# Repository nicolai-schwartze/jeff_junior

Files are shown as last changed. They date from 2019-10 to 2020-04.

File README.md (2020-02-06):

# Jeff Junior
This project is part of the FHV Master-Mechatronics course Applied Robotics. 

A 3-axis robot is equipped with 2 cameras and a red laser pointer. 
The robot looks for a green laser dot on a white flip-chart. 
When the green dot is found, the robot aims its red laser at the same position.

The work of this project includes everything, from the design and construction of the robot
to development of the backwards kinematic and computer vision. 

We build this robot on the libraries of:
*	[Dynamixel](https://github.com/ROBOTIS-GIT/DynamixelSDK)
*	[OpenCV](https://opencv.org/)

The backwards kinematic is implemented in C. 
These functions are provided in a dll. 
The computer vision is implemented in python. 

Fun Fact: 
The name originates from a fellow student who (jokingly) insisted, that we bought the robot 
on amazon and ultimately did no work for this project by ourself.

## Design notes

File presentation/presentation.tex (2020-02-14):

\documentclass{beamer}
\usepackage[utf8]{inputenc}

% Beamer Theme, might adapt
% https://hartwork.org/beamer-theme-matrix/
\usetheme{Madrid}
\usecolortheme{beaver}

%for colours e.g. \colorbox
\PassOptionsToPackage{usenames,dvipsnames}{xcolor}
\usepackage{xcolor}

%tables
\usepackage{longtable}
\usepackage{tabularx} 

\newcommand{\linebreakcellright}[2][c]{%
	\begin{tabular}[#1]{@{}r@{}}#2\end{tabular}}

\newcommand{\linebreakcellleft}[2][c]{%
	\begin{tabular}[#1]{@{}l@{}}#2\end{tabular}}

\newcommand{\linebreakcellcentre}[2][c]{%
	\begin{tabular}[#1]{@{}c@{}}#2\end{tabular}}

%Inline Code Snippets
\usepackage{listings}
\usepackage{color}

\definecolor{mygreen}{rgb}{0,0.6,0}
\definecolor{mygray}{rgb}{0.5,0.5,0.5}
\definecolor{mymauve}{rgb}{0.58,0,0.82}

\lstset{ 
	backgroundcolor=\color{white},   % choose the background color; you must add \usepackage{color} or \usepackage{xcolor}; should come as last argument
	basicstyle=\small,        % the size of the fonts that are used for the code
	breaklines=true,                 % sets automatic line breaking
	commentstyle=\color{mygreen},    % comment style
	extendedchars=true,              % lets you use non-ASCII characters; for 8-bits encodings only, does not work with UTF-8
	keepspaces=true,                 % keeps spaces in text, useful for keeping indentation of code (possibly needs columns=flexible)
	keywordstyle=\color{blue},       % keyword style
	language=Octave,                 % the language of the code
	morekeywords={parfor,pararrayfun, innerES},            % if you want to add more keywords to the set
	numbersep=5pt,                   % how far the line-numbers are from the code
	numberstyle=\tiny\color{mygray}, % the style that is used for the line-numbers
	rulecolor=\color{black},         % if not set, the frame-color may be changed on line-breaks within not-black text (e.g. comments (green here))
	showspaces=false,                % show spaces everywhere adding particular underscores; it overrides 'showstringspaces'
	showstringspaces=false,          % underline spaces within strings only
	showtabs=false,                  % show tabs within strings adding particular underscores
	stepnumber=1,                    % the step between two line-numbers. If it's 1, each line will be numbered
	stringstyle=\color{mymauve},     % string literal style
	tabsize=2,	                   	 % sets default tabsize to 2 spaces
}

% for pseudocode
\usepackage{amsmath}
\usepackage{algorithm}
\usepackage[noend]{algpseudocode}
\makeatletter
\def\BState{\State\hskip-\ALG@thistlm}
\makeatother

\title[jeff\textunderscore junior]{3 Axis Robot following a Laserpointer by using Stereovision and Templatematching}

\author[jwu, nsc]{Johannes Wüstner, Nicolai Schwartze}

\date{\today}

\begin{document}
\maketitle

\section{Introduction}
\frame{\tableofcontents}

\begin{frame}{Project Description}

\begin{itemize}
	\item construct a 3-axis robot with camera/laser tool
	\item calculate the backwards kinematic 
	\item program robot functions in C-DLL
	\item calibrate 3D camera system
	\begin{itemize}
		\item camera projection matrix
		\item hand-eye calibration
	\end{itemize}
	\item detect laser point on white flip-chart
	\item computer vision using OpenCV and Python
	\item drive with red robot laser to green user laser
\end{itemize}

\end{frame}

\section{Design}
\frame{\tableofcontents[currentsection]}

\begin{frame}{Task}
\begin{itemize}
	\item design a 3-axis robot in SolidWorks \\
	\item assemble the parts \\
	\item using Dynamixel MX-64AT motors \\
	\item attach camera/laser tool \\
\end{itemize}

\end{frame}

\begin{frame}{Result}

\begin{center}
	\begin{tabular}{ c c }
		   & 
		   
	\end{tabular}
\end{center}

\end{frame}

\section{Calculation}
\frame{\tableofcontents[currentsection]}

\begin{frame}{Task}

\begin{itemize}
	\item generate robot-backwards kinematic \\
	\item develop equation for setting angle of motor \\
	\item establish transformation matrix for hand-eye coordination \\
\end{itemize}

\end{frame}

\begin{frame}{Problem}

\begin{itemize}
	\item backwards kinematic
	\begin{itemize}
		\item establish DH parameter $\rightarrow$ transformation matrix TCP to robot base
	\end{itemize}
	\item setting motor angle
	\begin{itemize}
		\item only need two DOF $\rightarrow$ overdetermined
	\end{itemize}
	\item hand-eye coordination
	\begin{itemize}
		\item estimate the right distance camera to TCP
	\end{itemize}
\end{itemize}

\end{frame}

\begin{frame}{Solution I}

\begin{columns}[T] % align columns
	\begin{column}{.48\textwidth}
		\begin{center}
			
		\end{center}
		
	\end{column}%
	\hfill%
	\begin{column}{.45\textwidth}
		~\\~\\~\\
		\begin{center}
			\begin{tabular}{ c c c c c }
				$i$ & $\alpha_{i-1}$ & $a_{i-1}$ & $d_i$ & $\theta_{i-1}$\\ 
				\hline
				1 & 0 & 0 & 100 & $\theta_0$\\  
				2 & -90 & 50 & 0 & $\theta_1 - 90$\\ 
				3 & 0 & 100 & 0 & $\theta_2 + 180$\\ 
				F & 90 & 0 & 68 & $0$
			\end{tabular}
		\end{center}

	\end{column}%
\end{columns}

\end{frame}

\begin{frame}{Solution II}

\begin{equation}
\theta_0 = arctan(\frac{Y_0}{X_0})
\end{equation}

\begin{equation}
\theta_1 = 0.0
\end{equation}

\begin{equation}
\theta_2 = -1 \cdot arctan \left( \frac{ Z_0 - 100 - 100 cos(\theta_1)}{\sqrt{X_{0}^{2} + Y_{0}^{2}} - 50 - 100 sin(\theta_1)} \right)
\end{equation}

\end{frame}

\section{Camera Calibration}
\frame{\tableofcontents[currentsection]}

\begin{frame}{Task}

\begin{itemize}
	\item calculate camera matrix for both single cameras \\
	\item estimate translation and rotation between cameras \\
\end{itemize}

\end{frame}

\begin{frame}{Problem}

\begin{itemize}
	\item unstable against repetition \\
	\item chessboard must not have the same hight and width \\
	\item three quality control measures: 
	\begin{itemize}
		\item plausibility: translation vector between cameras
		\item measure actual 3D points 
		\item comparison with matlab
	\end{itemize}
\end{itemize}

\end{frame}

\begin{frame}{Solution}
\begin{center}

\end{center}
\end{frame}

\section{Laser Point Detection}
\frame{\tableofcontents[currentsection]}

\begin{frame}{Task}

\begin{itemize}
	\item detect green laser point
	\item detect red laser point (not used; would be helpful for controller)
\end{itemize}

\end{frame}

\begin{frame}{Problem}

\begin{itemize}
	\item first idea: use threshold for colour of laser
	\item detect contour 
	\item calculate centre of mass 
	\item problem: unstable against other lighting conditions
	\bigskip
	\item red laser point too small
	\item use laser with adjustable focal length 
\end{itemize}

\end{frame}

\begin{frame}{Solution}

\begin{itemize}
	\item use template matching
	\item created template calibration app before every run
	\item more stable against lighting conditions
	\item but can only work on specified background (like a flip-chart)
\end{itemize}
~\\
using the CV\textunderscore TM\textunderscore CCOEFF\textunderscore NORMED

\begin{equation}
R(x,y) = \frac{\sum_{x',y'} (T'(x',y') \cdot I'(x + x', y + y'))}{\sqrt{\sum_{x',y'} T'(x',y')^{2} \cdot \sum_{x',y'} I'(x + x', y + y')^{2}}}
\end{equation}
~\\
also works for coloured images, this equation is applied for every channel

\end{frame}

\section{Conclusion, Further Work}
\frame{\tableofcontents[currentsection]}

\begin{frame}{Summary, Further Work}

\begin{itemize}
	\item works (sort of) but slow convergence
	\item overshooting 
	\item resting offset 
	\item not using $\theta_1$
	\item 3 USB ports needed - opencv does not find camera on hub
	\item red laser uses loads of batteries $\frac{220 mAh}{45 mA} = 4.8 h$
	\bigskip
	\item implement controller 
	\item correct laser offset to align with axis $\theta_2$
	\item use undistort before calculateing 3D point
	\item power supply for laser
\end{itemize}

\end{frame}

\end{document}

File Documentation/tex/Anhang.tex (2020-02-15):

\documentclass[./\jobname.tex]{subfiles}
\begin{document}

\chapter{Drawings}

\includepdf[page=-]{../img/pdf/AKT L 3x30x80x30.pdf}
\includepdf[page=-]{../img/pdf/AKT U 3x48x40x48x90.pdf}
\includepdf[page=-]{../img/pdf/AKT U 3x73x46x73x90.pdf}
\includepdf[page=-]{../img/pdf/AKT Z 3x40x20x42_5x50.pdf}

\chapter{Motor Parameters}

\begin{table}[H]
	\centering
	\noindent\adjustbox{max width=\linewidth}{
		\begin{tabular}{|c|c|c|c|}
			\hline
			parameter & axis 0 & axis 1 & axis 2 \\
			\hline
			home offset & 2288 & 2060 & 3074 \\
			\hline
			min angle & 1580 & 2060 & 1650 \\
			\hline
			max angle & 3000 & 3200 & 3100 \\
			\hline
			max velocity & 20 & 20 & 20 \\
			\hline
			home & 2290 & 2060 & 3072 \\
			\hline
		\end{tabular}
	}
	\unterschrift{table of motor parameters}{}{}
	\label{tab:motor_param}
\end{table}

\end{document}

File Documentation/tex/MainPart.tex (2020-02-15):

% !TeX spellcheck = <none>
\documentclass[./\jobname.tex]{subfiles}

\begin{document}
\definecolor{light-gray}{gray}{0.9}

\chapter{Task Description}

This project is about constructing and building a 3-axis robot. The robot is equipped with two cameras and a red laser-pointer. The user can take a green laser-pointer to direct the robot into a different position. In order to avoid permanent sight-damage, the robot should avoid shining the laser into faces of surrounding humans. The following list contains the main working steps:

\begin{itemize}
	\item design and construct the 3-axis robot 
	\item manufacture and assemble the robot parts 
	\item develop the backwards kinematic 
	\item implement the backwards kinematic in C and compile to DLL 
	\item find green laser point in 3D stereo image with OpenCV in Python 
	\item drive the red laser point of the robot to the green laser point of the human
	\item planned but optional: 
	\begin{itemize}
		\item plan path from current position to green laser position 
		\item implement controller to correct deviance between red and green laser point 
		\item avoid human faces along the way
	\end{itemize}
	
\end{itemize}

\chapter{Design}

The robot consists of 3 Dynamixel MX-64AT motors, 2 Microsoft HD 3000 lifecam and a laser module DB635-1-3-FA(14x45)-ADJ from Picotronic. Aluminium frames are attached to the motors to build the framework of the robot. The cameras and laser-pointer are connected with aluminium brackets to the robot. The design of the robot and its components is established with SolidWords. The whole robot is mounted on aluminium profiles to improve the handling and to store of the electrical hardware. Beside the cables, a power supply for the motors and laser pointer, an emergency stop button and communication components for the motors are required. The cameras are directly connected to the laptop or computer via the USB ports. This means that the laptop requires 3 USB sockets. A connection via a USB-Hub failed as the OpenCV library could not find the cameras. \\
The table \ref{tab:camera_before_after} shows how the cameras were modified in order to properly attach them to the robot tool. \\
The table \ref{tab:3d_rander} displays a 3D render of the completely assembled robot.\\
Finally, the finished robot can be seen in figure \ref{fig:final_assemgly}

\begin{table}[H]
	\centering
	\noindent\adjustbox{max width=\linewidth}{
		\begin{tabular}{c c}
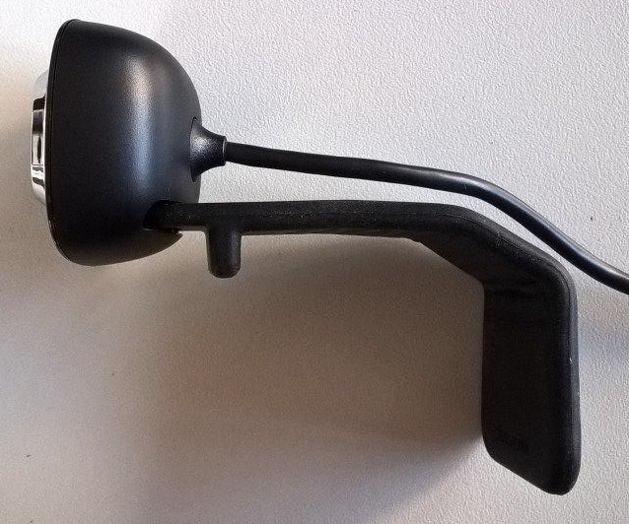
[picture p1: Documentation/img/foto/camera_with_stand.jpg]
			
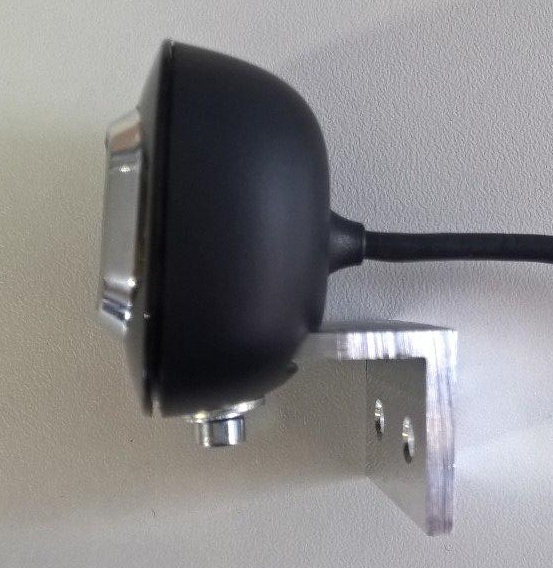
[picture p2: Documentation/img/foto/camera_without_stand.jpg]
			
		\end{tabular}
	}
	\unterschrift{comparison of the cameras before and after modification}{}{}
	\label{tab:camera_before_after}
\end{table}

\begin{table}[H]
	\centering
	\noindent\adjustbox{max width=\linewidth}{
		\begin{tabular}{c c}
			
			
		\end{tabular}
	}
	\unterschrift{3D render of the assembled robot in SolidWorks}{}{}
	\label{tab:3d_rander}
\end{table}

\begin{figure}[H]
	\centering
	\noindent\adjustbox{max width=\linewidth}{
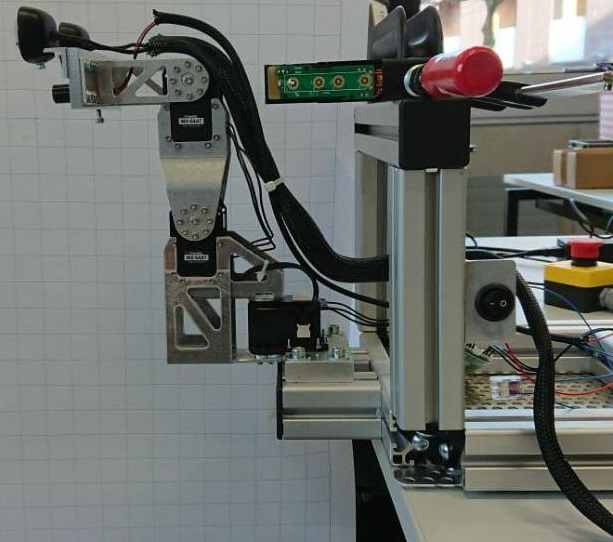
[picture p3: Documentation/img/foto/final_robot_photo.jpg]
		
	}
	\unterschrift{final assembly of the robot}{}{}
	\label{fig:final_assemgly}
\end{figure}

\chapter{Calculation}
This chapter describes the mathematical formulations that are needed to control the robot. This includes the backwards kinematics as well as the formulas for setting $\theta_{0,1,2}$. 

\section{Backwards Kinematic}

The following figure \ref{fig:robot_coord} shows the coordinate systems that are used to get the link parameters shown in table \ref{tab:link_params} below. The link parameters are established using the Deviant Hartenberg convention mentioned in \cite[p. 70- 79]{Craig2018}.

With the knowledge of the link parameters, the transformation matrices are generated in the next step. The full matrix can be seen in equation \ref{eq:transformationmatrix}

\begin{figure}[H]
	\centering
	\noindent\adjustbox{max width=\linewidth}{
		
	}
	\unterschrift{robot axis coordinate systems used to calculate the link parameters}{}{}
	\label{fig:robot_coord}
\end{figure}

\begin{table}[H]
	\centering
	\noindent\adjustbox{max width=\linewidth}{
		\begin{tabular}{|c|c|c|c|c|}
			\hline
			$i$ & $\alpha_{i-1}$ & $a_{i-1}$ & $d_i$ & $\theta_{i-1}$\\ 
			\hline
			1 & 0 & 0 & 100 & $\theta_0$\\  
			2 & -90 & 50 & 0 & $\theta_1 - 90$\\ 
			3 & 0 & 100 & 0 & $\theta_2 + 180$\\ 
			F & 90 & 0 & 68 & $0$ \\
			\hline
		\end{tabular}
	}
	\unterschrift{table of link parameters}{}{}
	\label{tab:link_params}
\end{table}

\begin{equation}
\label{eq:transformationmatrix}
\begin{split}
& T =  \\
& \begin{bmatrix}
-c0c1s2 -c0c2s1 & -s0 & c0c1c2 - c0s1s2 & a2c0 + dF (c0c1c2 - c0s1s2) + a3c0s1 \\
-c1s0s2 -c2s0s1 &  c0 & c1c2s0 - s0s1s2 & a2s0 + dF (c1c2s0 - s0s1s2) + a3s0s1 \\
s1s2 - c1c2     &   0 & -c1s2 - c2s1 & d1 + a3c1 + dF(-c1s2 - c2s1) \\
0               &   0 & 0 & 1 \\
\end{bmatrix}\\
\end{split}
\end{equation}

\subsection{Implementation}
For controlling the robot, several functions are written in C and compiled to a DLL. The functions are built on the Dynamixel library \cite{Robotis2019}. The DLL provides the following methods: 
\begin{itemize}
	\item \colorbox{light-gray}{\lstinline[basicstyle=\ttfamily\color{black}]|int robot_start();|} \\
	Sets up the communication with the robot by returning the port number. This number must be provided in every other function. Further this function sets up the main parameters of every motor like the velocity limits.
	\item \colorbox{light-gray}{\lstinline[basicstyle=\ttfamily\color{black}]|void robot_stop(int port_num);|} \\ 
	Stops the robot by driving to the home position and freeing the device with the port number. 
	\item \colorbox{light-gray}{\lstinline[basicstyle=\ttfamily\color{black}]|void robot_home(int port_num);|} \\
	Separate function for driving the robot to the home position. 
	\item \colorbox{light-gray}{\lstinline[basicstyle=\ttfamily\color{black}]|int robot_drive(float z, float alpha, float beta, int port_num);|} \\
	Tells the robot to drive to a specific position specified by $\alpha$, $\beta$ and z. The motion towards this position is not planned. 
	\item \colorbox{light-gray}{\lstinline[basicstyle=\ttfamily\color{black}]|int robot_reached_target(float z, float alpha, float beta, \ \ \ \ \ int port_num);|} \\
	This function checks if the robot is at the specified $\alpha$, $\beta$ and z position and returns 1 if it reached the target (otherwise 0).
	\item \colorbox{light-gray}{\lstinline[basicstyle=\ttfamily\color{black}]|void robot_set_theta(float theta0, float theta1, float theta2, \ \ \ \ \ int port_num);|} \\
	Instead of specifying a global position, this function allows to set the axis angle $\theta$ by its own. 
	\item \colorbox{light-gray}{\lstinline[basicstyle=\ttfamily\color{black}]|float robot_get_theta0(int port_num);|} \\
	Returns the angle $\theta_0$ that the robot is at that time.
	\item \colorbox{light-gray}{\lstinline[basicstyle=\ttfamily\color{black}]|float robot_get_theta1(int port_num);|} \\
	Returns the angle $\theta_1$ that the robot is at that time.
	\item \colorbox{light-gray}{\lstinline[basicstyle=\ttfamily\color{black}]|float robot_get_theta2(int port_num);|} \\ 
	Returns the angle $\theta_2$ that the robot is at that time.
\end{itemize}
The functions \textit{robot\textunderscore drive} as well as the function \textit{robot\textunderscore set\textunderscore theta} are non-blocking. This means that the function returns, before the robot reached the target. Blocking functions can be easily created outside the DLL by simply polling the functions \textit{robot\textunderscore reached\textunderscore target} or \textit{robot\textunderscore get\textunderscore theta}.  

\section{Goal Robot Configuration}
\label{sec:calc_robot_config}

The laser point on the wall can be described by only to 2 DOF, vertical and horizontal coordinates. To track the laser point, the robot has to change 2 DOF likewise. Even though the robot has 3 rotation axis, it only satisfy 2 DOF, because $theta_1$ and $theta_2$ directly depend to each other. Therefore, one of these angles can be set to any arbitrary angle. In this case $theta_1$ is constantly set to 0°. With the 2 cameras and the knowledge of the transformation matrices of the robot, the vertical and horizontal coordinates of the laser point are received and transformed into 3D coordinates of the robot base coordinate system.

As a result, the rotation angle of the motors can be calculated. $\theta_0$ is a simple geometric problem and can be easily calculated with trigonometric functions (see figure \ref{fig:3d_point_base}). The equation \ref{eq:theta_2} for $\theta_2$ is slightly more advanced. Additionally, the length and height of the robot components have to be taken in consideration.

\begin{figure}[H]
	\centering
	\noindent\adjustbox{max width=\linewidth}{
		
	}
	\unterschrift{camera calibration app flowchart}{}{}
	\label{fig:3d_point_base}
\end{figure}

\begin{equation}
\label{eq:theta_0}
\theta_0 = arctan \left( \frac{Y_0}{X_0} \right) 
\end{equation}

\begin{equation}
\label{eq:theta_2}
\theta_2 = -1 \cdot arctan \left( \frac{ Z_0 - 100 - 100 cos(\theta_1)}{\sqrt{X_{0}^{2} + Y_{0}^{2}} - 50 - 100 sin(\theta_1)} \right)
\end{equation}

\chapter{Stereo Vision}

The idea of this project is to drive directly to the correct point, without using a closed loop controller of any sort. This is done by measuring the 3D point with a stereo camera and calculating back to the desired robot configuration (as shown in \ref{sec:calc_robot_config}). In order to measure the correct point, the cameras need to be calibrated. Further, a reliable method for finding the laser-point is needed. All vision related tasks are done with \cite{2014opencv}

\section{Camera Calibration}
At first a camera calibration application is written, that allows to take images, calculate the two single camera matrices and estimates the translation and rotation between the two cameras. The flowchart in figure \ref{fig:cam_cal_app_flowchart} shows the main outline of the camera calibration app. 

Three quality measures are deployed to verify that the matrices are correct: 
\begin{itemize}
	\item measuring a known 3D structure with the calibrated stereo camera tool
	\item using the same pictures of the chessboard in MATLAB and comparing the calculated matrices
	\item plausibility check for the translation vector and the rotation matrix between the cameras
\end{itemize}

Besides the camera calibration towards each other, the main camera (left) must also be calibrated to the TCP. This is called the hand-eye calibration. The following matrix \ref{eq:HE} shows the hand-eye calibration. Although there are more complex methods to generate this transformation matrix, it can also be measured from the real tool. The figure \ref{fig:hand_eye_coord} shows the rotation between the TCP coordinate system and the camera coordinate system.

\begin{equation}
\label{eq:HE}
HE = 
\begin{bmatrix}
0.0  & 1.0 & 0.0 & -28.5 \\ 
-1.0 & 0.0 & 0.0 & 45.0 \\
0.0  & 0.0 & 1.0 & 28.0 \\ 
0.0  & 0.0 & 0.0 & 1.0 \\
\end{bmatrix}
\end{equation}

\begin{figure}[h]
	\centering
	\noindent\adjustbox{max width=\linewidth}{
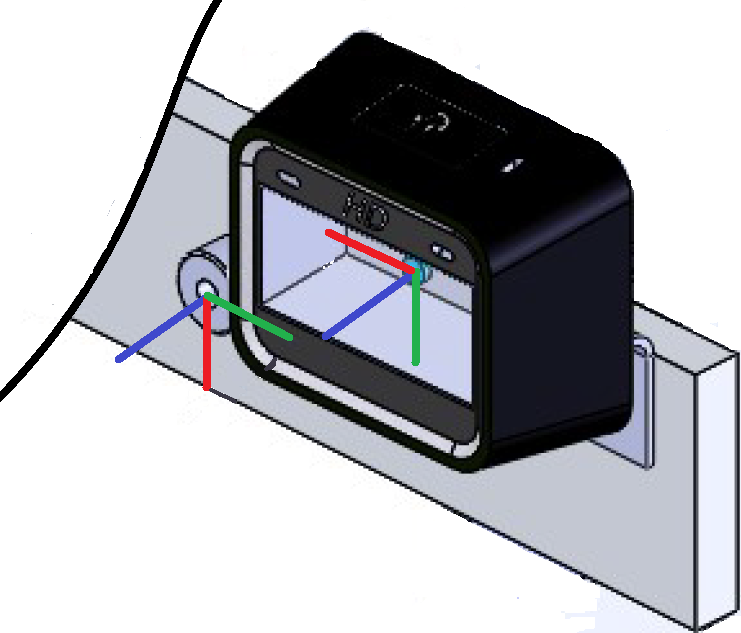
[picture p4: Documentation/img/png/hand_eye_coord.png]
		
	}
	\unterschrift{hand-eye coordinate system transformation}{}{}
	\label{fig:hand_eye_coord}
\end{figure}

\begin{figure}[h]
	\centering
	\noindent\adjustbox{max width=\linewidth}{
		
	}
	\unterschrift{camera calibration app flowchart}{}{}
	\label{fig:cam_cal_app_flowchart}
\end{figure}

\section{Laser Point Detection}
The second part is about detecting the laser point in an image. To make the task simpler, the laser point may only be projected onto a white flip board chart. \\
Two methods for detecting the laser point are tested. 

\subsection{Method 1: HSV Threshold}
As lasers are monochromatic one could think about looking for a certain colour. The idea is to define a threshold in HSV-colour space and only look at the pixels that are within this band. By applying a dilation function to the binary image, the weakly connected pixels are morphed together and form blobs. Then the function \textit{findCountours} is deployed to detect the connected areas of white pixels. Finally, the first (biggest) area contour is taken and the centre of mass is calculated. This is the 2D point in one image. \\
This method did not work very well. Some problems have been identified: 
\begin{itemize}
	\item Taking the biggest area is not very sensible. More constraints could be helpful like: size threshold, convexity or previous point.
	\item As the automatic mode of the camera is not deactivated the colour of the laser point might change with different lighting scenarios. 
	\item The definition of the colour threshold is not trivial: Either too many pixels or too few are taken. Especially with a colourful surrounding this trade-off is hard to control. 
\end{itemize}

\subsection{Method 2: Template Matching}

The second method uses template matching to find the green laser point. The process outline as follows: a template slides over the image and at every pixel they are compared. The comparison results a scalar value which are then stacked together to create something like a `heat-map'. The larger the scalar is at an index, the better is the correspondence between the image and the template. \\
There are many different methods for comparing two images defined in OpenCV. The utilize method was found to work best for this sort of object detection. The formula is shown in equation \ref{eq:template_matching}. \\
The templates are created before every run. In order to make that process as user-friendly as possible, a GUI based configuration app is created. The templates can be seen in the table \ref{tab:laser_template_comp}. \\
The main characteristics of this method are: 
\begin{itemize}
	\item This method works much better with different lighting scenarios than the HSV-threshold.
	\item Motion blurring results in an unstable detection of the laser point. Thus, fast movements with the robot and by hand should be avoided. 
	\item Whenever there is no green laser point in the image, the red laser is detected as green, since this is now the best match. 
	\item This method only works with the background (e.g. white flip board) specified in the template. 
\end{itemize} 

\begin{equation}
R(x,y) = \frac{\sum_{x',y'} (T'(x',y') \cdot I'(x + x', y + y'))}{\sqrt{\sum_{x',y'} T'(x',y')^{2} \cdot \sum_{x',y'} I'(x + x', y + y')^{2}}}
\label{eq:template_matching}
\end{equation}

\begin{table}[h]
	\centering
	\noindent\adjustbox{max width=\linewidth}{
		\begin{tabular}{c c}
			
			
		\end{tabular}
	}
	\unterschrift{laser point template as created by the configuration app}{}{}
	\label{tab:laser_template_comp}
\end{table}

\chapter{Main App}
This chapter describes the algorithmic steps taken in the main application as seen in the flowchart \ref{fig:main_app_flowchart}. The action \textit{transform 3D point to robot base} consists of multiple steps itself: 

\begin{itemize}
	\item Multiply the 3D point with the hand-eye calibration to transform the point into the TCP frame, as seen in \ref{eq:HE} 
	\item Transform the point to the robot base coordinate system by multiplying with the backwards kinematic in \ref{eq:transformationmatrix}. 
\end{itemize}

\begin{figure}[h]
	\centering
	\noindent\adjustbox{max width=\linewidth}{
		
	}
	\unterschrift{camera calibration app flowchart}{}{}
	\label{fig:main_app_flowchart}
\end{figure}

\chapter{Conclusion}

We find, that template matching method is better suited to detect small objects in a constantly changing image rather than searching the images for a specific colour.

The resting distance between green and red laser point, as seen in figure \ref{fig:resting_offset} results from the offset of the laser pointer to the robot tool centre. That can be easily adjusted with a new bracket. To avoid any systematic errors, the laser pointer has to be mounted colinear with the z-axis of the robot tool.  

Another current problem is the high energy consumption of the laser pointer. Within a half an hour, the intensity of the laser pointer dropped significantly. In the next step, a more appropriate power supply should be installed.

An additional option could be to specify $theta_1$ as a variable instead of a constant and find a more advanced system of equations.   

\begin{figure}[H]
	\centering
	\noindent\adjustbox{max width=\linewidth}{
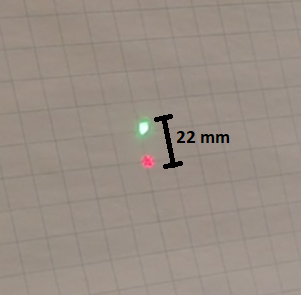
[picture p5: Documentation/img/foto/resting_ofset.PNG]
		
	}
	\unterschrift{resting offset between laser points}{}{}
	\label{fig:resting_offset}
\end{figure}

\end{document}

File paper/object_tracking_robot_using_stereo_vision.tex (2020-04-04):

\documentclass[11pt,twoside,twocolumn,a4paper]{article}

\usepackage{acvrw}
\usepackage{times}
\usepackage{epsfig}
\usepackage{graphicx}
\usepackage{amsmath}
\usepackage{amssymb}
\usepackage{url}
\usepackage{float}

\newcommand\scalemath[2]{\scalebox{#1}{\mbox{\ensuremath{\displaystyle #2}}}}

%%%%%%%%%%%%%%%
%% FINAL COPY %
%%%%%%%%%%%%%%%

% !!! UNCOMMENT THIS LINE FOR THE FINAL SUBMISSION !!!
% \acvrwfinalcopy 

\def\acvrwPaperID{20} % *** Enter the ACVRW Paper ID here
\def\httilde{\mbox{\tt\raisebox{-.5ex}{\symbol{126}}}}

% Pages are numbered in submission mode, and unnumbered in camera-ready
\ifacvrwfinal\pagestyle{empty}\fi
\begin{document}

%%%%%%%%%
% TITLE %
%%%%%%%%%
\title{Object Tracking Robot using Stereo Vision}

\author{Nicolai Schwartze, Johannes Wüstner\\
FH Vorarlberg University of Applied Science\\
{\tt\small \{nicolai.schwartze,johannes.wuestner\}@students.fhv.at}
}

\maketitle
\ifacvrwfinal\thispagestyle{fancy}\fi

%%%%%%%%%%%%
% ABSTRACT %
%%%%%%%%%%%%

\begin{abstract}
This paper originates from a coursework done in the module Applied Robotics at the Vorarlberg University of Applied Science (FH Vorarlberg). The work is about finding a green laser point on a white flip-board chart. A robot with a 3D camera system tracks this point and drives its laser-pointer tool to the same spot. The premiss was not to use any position controller and instead compute the desired axis-angles from the 3D information of the found laser dot. The paper describes the design and the implementation of the system. 
\end{abstract}

%%%%%%%%%%%%%
% BODY TEXT %
%%%%%%%%%%%%%

%-------------------------------------------------------------------------
\section{Task Constrains}

The following requirements were posed to fulfil this coursework: 
\begin{itemize}
\item Create a 3-axis robot and not a simple two-axis pan/tilt device. 
\item Measure the 3D point of the laser and drive to its position without using a closed loop controller. 
\end{itemize}

%-------------------------------------------------------------------------
\section{Design}

The robot consists of 3 Dynamixel MX-64AT motors, two Microsoft Lifecam HD 3000 (640x480 pixel) and a laser-pointer.
Aluminium frames are attached to the motors to build the framework of the robot. The cameras and laser-pointer are connected with aluminium brackets. The design of the robot and its components is established with SolidWorks.
Figure \ref{fig:3d-render} shows a 3D render of the fully assembled robot.

\begin{figure}[h]
	\centering
	
	\caption{3D render of the assembled robot}
	\label{fig:3d-render}
\end{figure}

%-----------------------------------------------------------------------------
\section{Robot Kinematic}

The motors can be controlled by a supplied library, which is written in C \cite{Robotis2019}. This allows us to write our own DLL to implement the backwards kinematics and control the robot as a whole. Figure \ref{fig:robot-axis-coord} shows the coordinate systems that are used to get the link parameters shown in table \ref{tab:link_parameter}. The link parameters are established using the Denavit Hartenberg convention mentioned in \cite[p. 70-79]{Craig2018}.

With the link parameters, the inverse kinematics matrix can be generated. This is used to transfer the 3D point captured by the camera, from the tool frame $\left\lbrace F \right\rbrace$  to the base coordinate system $\left\lbrace 0 \right\rbrace $. From there, the point can be transferred into the coordinate frame $\left\lbrace 3 \right\rbrace $. This transformation is implicitly included in equation (\ref{eq:theta2}). Together with (\ref{eq:theta0}) these equations can be used to calculate the desired robot configuration. 
Because $\theta_1$ and $\theta_2$ directly depend on each other, $\theta_1$ can be set to any arbitrary angle.

\begin{equation}
\label{eq:theta0}
\theta_0 = arctan \left(  \frac{P_{Y0}}{P_{X0}} \right) 
\end{equation}

\begin{equation}
\label{eq:theta2}
\theta_2 = - arctan \left( \frac{ P_{Z0} - 100 - 100 cos(\theta_1)}{\sqrt{P_{X0}^{2} + P_{Y0}^{2}} - 50 - 100 sin(\theta_1)} \right)
\end{equation}

\begin{table}[h]
	\centering
	\begin{tabular}{ | c | c | c | c | c | }
		\hline
		$i$ & $\alpha_{i-1}$ & $a_{i-1}$ & $d_i$ & $\theta_{i-1}$\\ 
		\hline \hline
		1 & 0 & 0 & 100 & $\theta_0$\\  
		2 & -90 & 50 & 0 & $\theta_1 - 90$\\ 
		3 & 0 & 100 & 0 & $\theta_2 + 180$\\ 
		F & 90 & 0 & 68 & $0$\\
		\hline
	\end{tabular}
	\caption{link parameter }
	\label{tab:link_parameter}
\end{table} 

\begin{figure}[h]
	\centering
	
	\caption{axis coordinate systems for computing the inverse kinematic}
	\label{fig:robot-axis-coord}
\end{figure}

%-------------------------------------------------------------------------------
\section{Tool Calibration}
The tool calibration includes three steps: Estimating the camera projection matrix as well as the transformation from the main camera (left in robot sight direction) to the TCP and the transformation of the laser pointer towards the TCP. 

\subsection{Hand-Eye Transformation Matrix}
The hand-eye calibration is measured from the real robot. It is assumed, that the rotation between the camera coordinate system and the tool is small. We only have to rotate the coordinate system and take the translation vector into account. Another method would be that of Park and Martin \cite{ParkHandEye} which is also provided in OpenCV. 

\begin{figure}[h]
	\centering
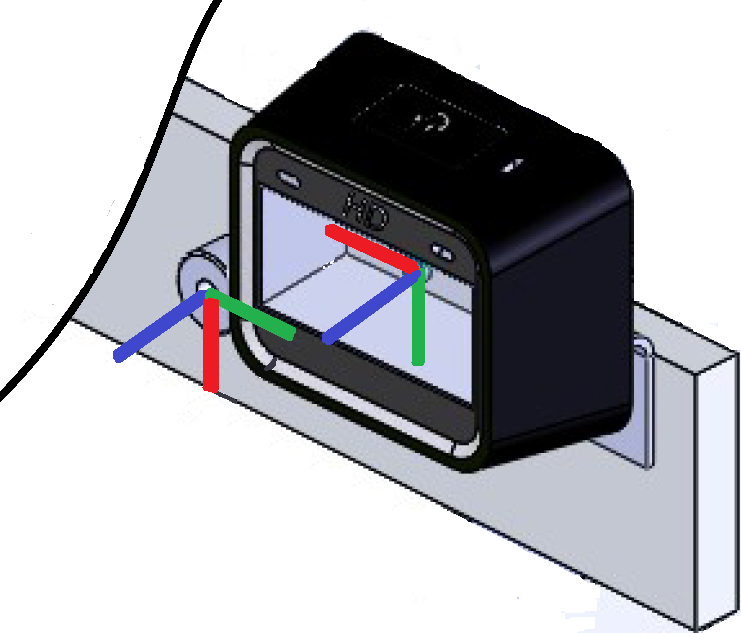
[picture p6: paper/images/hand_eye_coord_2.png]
	
	\caption{axis coordinate systems for computing the backwards kinematic}
	\label{fig:hand_eye_coord}
\end{figure}

\subsection{Laser Calibration}
Since the laser is designed to lay directly in line with the Z-coordinate of the tool frame, there is no calibration needed. This demands a fine level of accuracy for the manufacturing process. 

\subsection{Stereo Camera Projection Matrix}

The camera projection matrix is estimated from multiple images of the same chessboard calibration plate \cite[p. 178-182]{Ziss2008}. At first, the intrinsic parameters of both cameras are estimated separately using the OpenCV function \textit{calibrateCamera}. With this information the function \textit{stereoCalibrate} can be used to estimate the translation and rotation between the two cameras. With these matrices and the function \textit{triangulate} a 2D point correspondence can be associated with one 3D point. The camera calibration app is implemented in Python using these OpenCV functions \cite{2014opencv}. 

%-------------------------------------------------------------------------
\section{Object Detection}
Two methods for detecting the laser dot are tested.  \\
\textbf{Option 1:} use a HSV-threshold and only look for pixels with that specific value. This method is unstable against different illumination scenarios. \\
\textbf{Option 2:} use template matching with user-defined template. The main idea is to calculate a normalized difference between every pixel in the image and a template \cite[p. 1061-1062]{Gonz2018}. This function is called \textit{matchTemplate} and is also provided by OpenCV. The method \textit{CV\textunderscore TM\textunderscore CCOEFF\textunderscore NORMED} was found to work most reliable for multiple different lighting scenarios. This method uses the equation \ref{eq:template_matching} below, where $T$ stands for the template and $I$ is the image. 

\begin{equation}
R(x,y) = \frac{\sum_{x',y'} (T'(x',y') \cdot I'(x + x', y + y'))}{\sqrt{\sum_{x',y'} T'(x',y')^{2} \cdot \sum_{x',y'} I'(x + x', y + y')^{2}}}
\label{eq:template_matching}
\end{equation}

%-------------------------------------------------------------------------
\section{Result and Conclusion}
We can show that the described system works as specified. We find, that template matching is better suited to detect small objects in a constantly changing image rather than searching the images for a specific colour.  
Further steps could include to verify the assumption about the orientation of the laser tool as well as refining the hand-eye calibration. 

%-------------------------------------------------------------------------{\small
{\small
\bibliographystyle{ieee}
\bibliography{acvrw}
}

\end{document}

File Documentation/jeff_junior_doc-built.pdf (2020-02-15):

## Jeff Junior

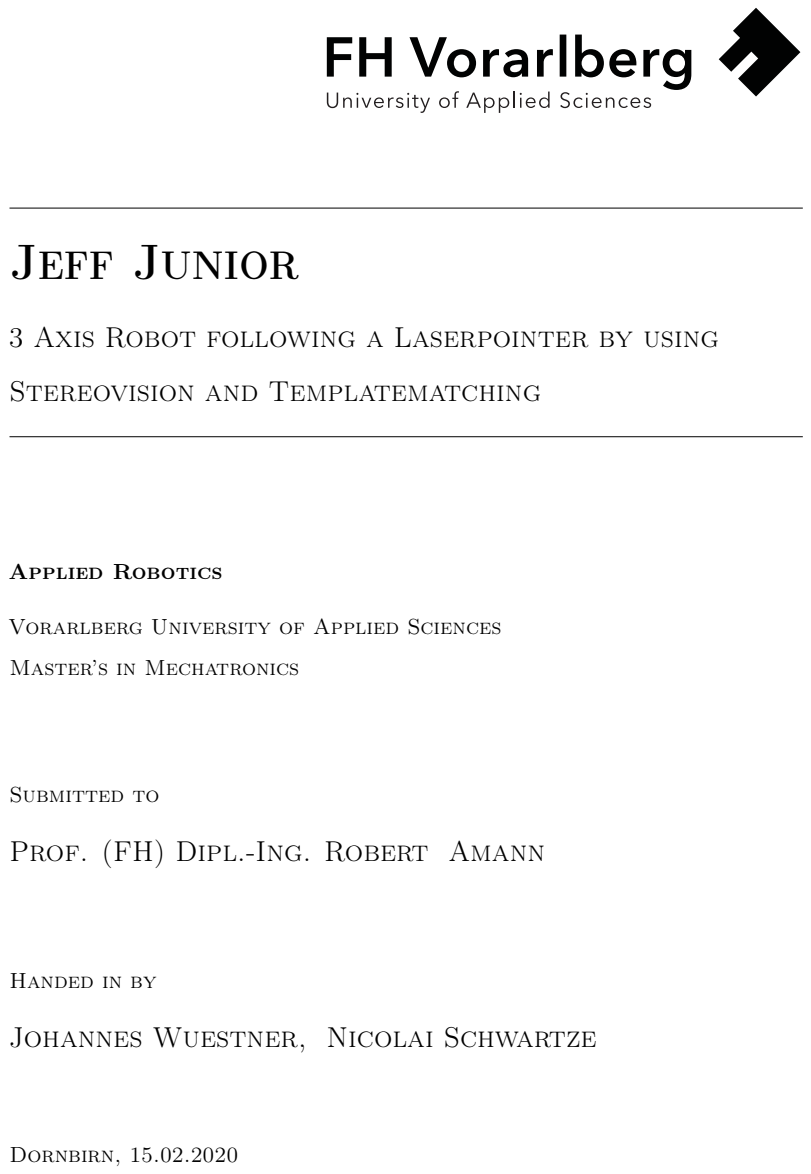
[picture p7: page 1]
Applied Robotics; Submitted to; Prof. (FH) Dipl.-Ing. Robert; Amann; Dornbirn, 15.02.2020

3 Axis Robot following a Laserpointer by using

Stereovision and Templatematching

Vorarlberg University of Applied Sciences

Master’s in Mechatronics

Handed in by

Johannes Wuestner, Nicolai Schwartze

# Contents

List of Figures | II
List of Tables | III
1 Task Description | 1
2 Design | 2
3 Calculation | 4
4 Stereo Vision | 8
5 Main App | 12
6 Conclusion | 14
Bibliography | 15
Appendices | 16
A Drawings | 17
B Motor Parameters | 22

I

# List of Figures

3.1 robot axis coordinate systems used to calculate the link parameters 4

II

# List of Tables

2.1 comparison of the cameras before and after modification | | 2
2.2 3D render of the assembled robot in SolidWorks | | 3
3.1 table of link parameters | | 5
4.1 laser point template as created by the configuration app | | 10

III

# 1 Task Description

This project is about constructing and building a 3-axis robot. The robot is equipped with two cameras and a red laser-pointer. The user can take a green laser-pointer to direct the robot into a different position. In order to avoid permanent sight-damage, the robot should avoid shining the laser into faces of surrounding humans. The following list contains the main working steps:

- design and construct the 3-axis robot
- manufacture and assemble the robot parts
- develop the backwards kinematic
- implement the backwards kinematic in C and compile to DLL
- find green laser point in 3D stereo image with OpenCV in Python
- drive the red laser point of the robot to the green laser point of the human
- planned but optional:

– plan path from current position to green laser position

– implement controller to correct deviance between red and green laser point

– avoid human faces along the way

1

# 2 Design

The robot consists of 3 Dynamixel MX-64AT motors, 2 Microsoft HD 3000 lifecam and a laser module DB635-1-3-FA(14x45)-ADJ from Picotronic. Aluminium frames are attached to the motors to build the framework of the robot. The cameras and laser-pointer are connected with aluminium brackets to the robot. The design of the robot and its components is established with SolidWords. The whole robot is mounted on aluminium profiles to improve the handling and to store of the electrical hardware. Beside the cables, a power supply for the motors and laser pointer, an emergency stop button and communication components for the motors are required. The cameras are directly connected to the laptop or computer via the USB ports. This means that the laptop requires 3 USB sockets. A connection via a USB-Hub failed as the OpenCV library could not find the cameras.
The table 2.1 shows how the cameras were modified in order to properly attach them to the robot tool.
The table 2.2 displays a 3D render of the completely assembled robot.
Finally, the finished robot can be seen in figure 2.1

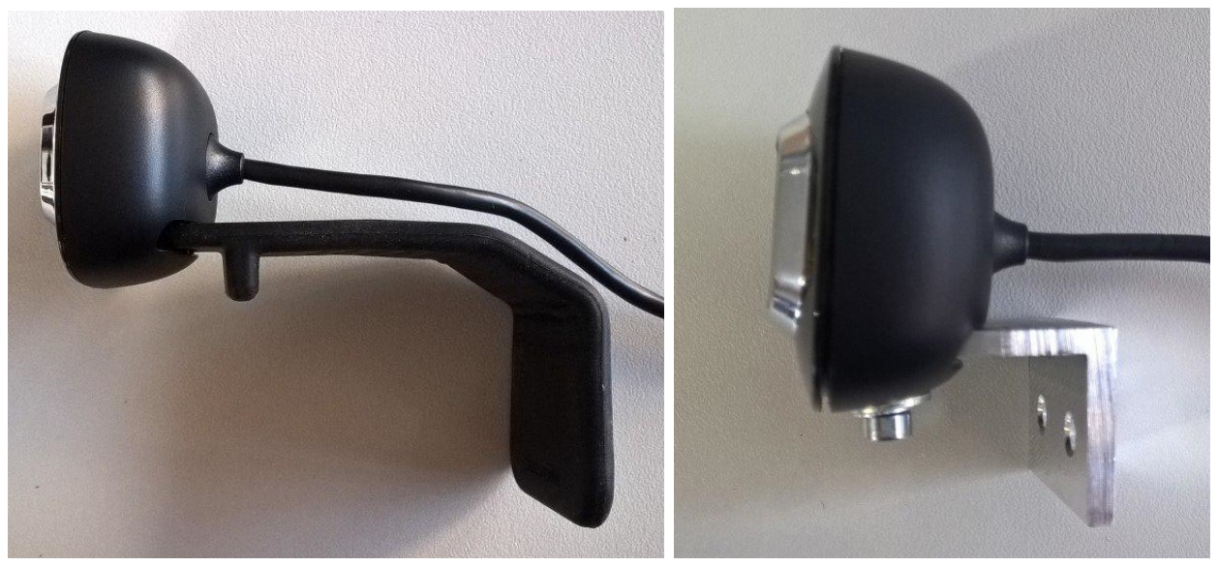
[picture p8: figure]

Table 2.1: comparison of the cameras before and after modification

2

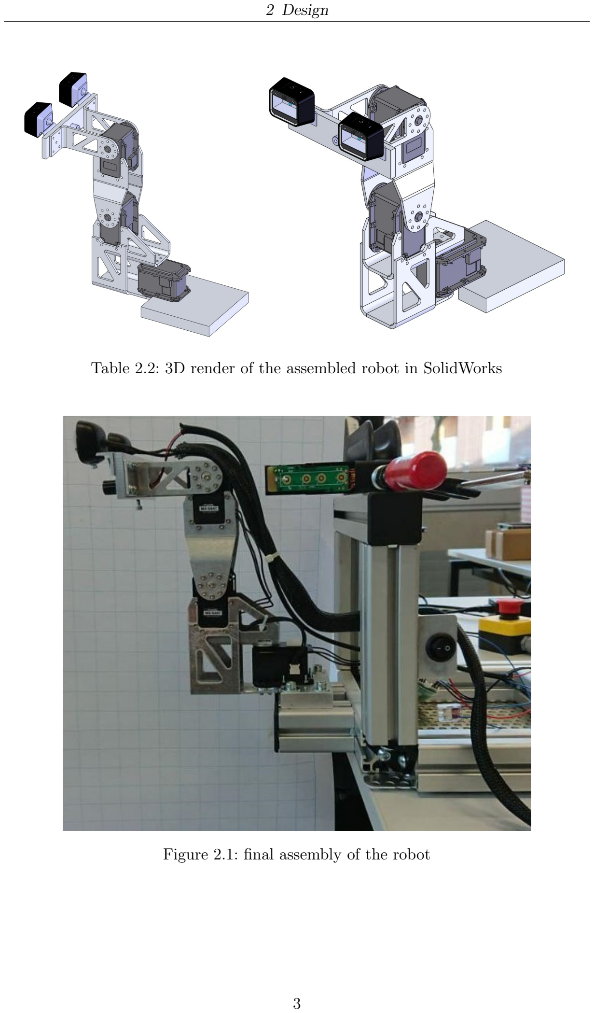
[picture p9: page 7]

2 Design

Table 2.2: 3D render of the assembled robot in SolidWorks

Figure 2.1: final assembly of the robot

3

# 3 Calculation

This chapter describes the mathematical formulations that are needed to control the robot. This includes the backwards kinematics as well as the formulas for setting

θ0,1,2.

## 3.1 Backwards Kinematic

The following figure 3.1 shows the coordinate systems that are used to get the link parameters shown in table 3.1 below. The link parameters are established using the Deviant Hartenberg convention mentioned in Craig 2018, p. 70- 79.

With the knowledge of the link parameters, the transformation matrices are generated in the next step. The full matrix can be seen in equation 3.1

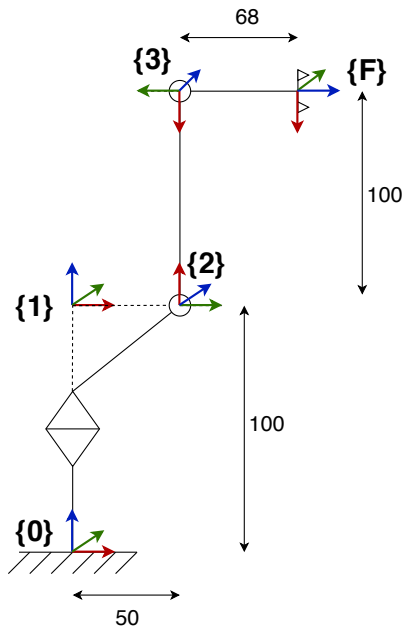
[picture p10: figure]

Figure 3.1: robot axis coordinate systems used to calculate the link parameters

4

3 Calculation

i | αi−1 | ai−1 | di | θi−1
1 2 3 F | 0 -90 0 90 | 0 50 100 0 | 100 0 0 68 | θ0 θ1 − 90 θ2 + 180 0

Table 3.1: table of link parameters

T =

−c0c1s2 − c0c2s1 −s0 c0c1c2 − c0s1s2 a2c0 + dF(c0c1c2 − c0s1s2) + a3c0s1
−c1s0s2 − c2s0s1 | c0 | c1c2s0 − s0s1s2 a2s0 + dF(c1c2s0 − s0s1s2) + a3s0s1
s1s2 − c1c2 | 0 | −c1s2 − c2s1 | d1 + a3c1 + dF(−c1s2 − c2s1)
0 | 0 | 0 | 1

| | | (3.1)

### 3.1.1 Implementation

For controlling the robot, several functions are written in C and compiled to a DLL. The functions are built on the Dynamixel library ROBOTIS-GIT 2019. The DLL provides the following methods:

- int robot_start();
Sets up the communication with the robot by returning the port number. This number must be provided in every other function. Further this function sets up the main parameters of every motor like the velocity limits.
- void robot_stop(int port_num);
Stops the robot by driving to the home position and freeing the device with the port number.
- void robot_home(int port_num);
Separate function for driving the robot to the home position.
- int robot_drive(float z, float alpha, float beta, int port_num); Tells the robot to drive to a specific position specified by α, β and z. The motion towards this position is not planned.

•

int robot_reached_target(float z, float alpha, float beta, int port_num);
This function checks if the robot is at the specified α, β and z position and returns 1 if it reached the target (otherwise 0).

5

3 Calculation

•

void robot_set_theta(float theta0, float theta1, float theta2, int port_num);
Instead of specifying a global position, this function allows to set the axis angle θ by its own.
- float robot_get_theta0(int port_num);
Returns the angle θ0 that the robot is at that time.
- float robot_get_theta1(int port_num); Returns the angle θ1 that the robot is at that time.
- float robot_get_theta2(int port_num);
Returns the angle θ2 that the robot is at that time.

The functions robot_drive as well as the function robot_set_theta are non-blocking. This means that the function returns, before the robot reached the target. Blocking functions can be easily created outside the DLL by simply polling the functions robot_reached_target or robot_get_theta.

## 3.2 Goal Robot Configuration

The laser point on the wall can be described by only to 2 DOF, vertical and horizontal coordinates. To track the laser point, the robot has to change 2 DOF likewise. Even though the robot has 3 rotation axis, it only satisfy 2 DOF, because theta1 and theta2 directly depend to each other. Therefore, one of these angles can be set to any arbitrary angle. In this case theta1 is constantly set to 0°. With the 2 cameras and the knowledge of the transformation matrices of the robot, the vertical and horizontal coordinates of the laser point are received and transformed into 3D coordinates of the robot base coordinate system.

As a result, the rotation angle of the motors can be calculated. θ0 is a simple geometric problem and can be easily calculated with trigonometric functions (see figure 3.2). The equation 3.3 for θ2 is slightly more advanced. Additionally, the length and height of the robot components have to be taken in consideration.

6

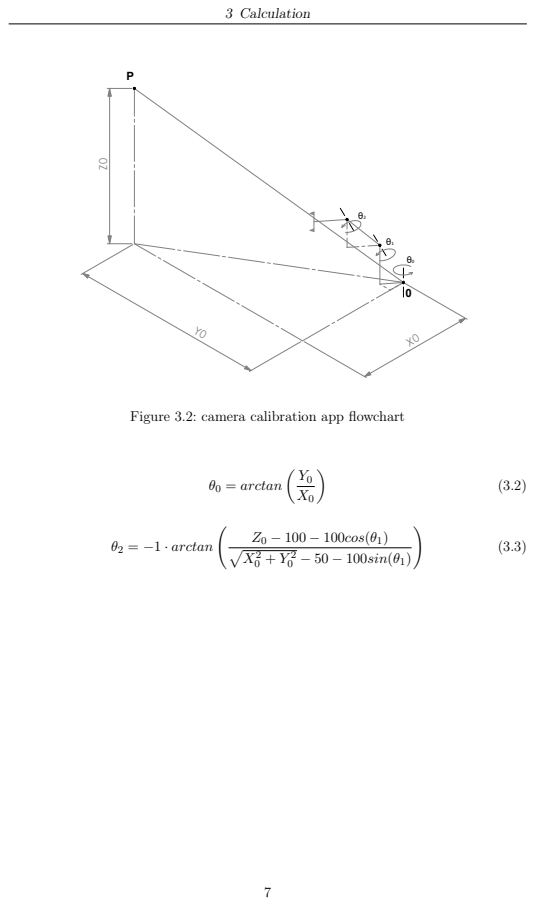
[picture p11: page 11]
3 Calculation; θ0 = arctan ; θ2 = −1 · arctan; Z0 − 100 − 100cos(θ1); 2 0 − 50 − 100sin(θ1)

Figure 3.2: camera calibration app flowchart

# 4 Stereo Vision

The idea of this project is to drive directly to the correct point, without using a closed loop controller of any sort. This is done by measuring the 3D point with a stereo camera and calculating back to the desired robot configuration (as shown in 3.2). In order to measure the correct point, the cameras need to be calibrated. Further, a reliable method for finding the laser-point is needed. All vision related tasks are done with The OpenCV Reference Manual 2019

## 4.1 Camera Calibration

At first a camera calibration application is written, that allows to take images, calculate the two single camera matrices and estimates the translation and rotation between the two cameras. The flowchart in figure 4.2 shows the main outline of the camera calibration app.

Three quality measures are deployed to verify that the matrices are correct:

- measuring a known 3D structure with the calibrated stereo camera tool
- using the same pictures of the chessboard in MATLAB and comparing the calculated matrices
- plausibility check for the translation vector and the rotation matrix between the cameras

Besides the camera calibration towards each other, the main camera (left) must also be calibrated to the TCP. This is called the hand-eye calibration. The following matrix 4.1 shows the hand-eye calibration. Although there are more complex methods to generate this transformation matrix, it can also be measured from the real tool. The figure 4.1 shows the rotation between the TCP coordinate system and the camera coordinate system.

HE =

0.0 | 1.0 0.0 −28.5
−1.0 0.0 0.0 | 45.0
0.0 | 0.0 1.0 | 28.0
0.0 | 0.0 0.0 | 1.0

(4.1)

8

4 Stereo Vision


Figure 4.1: hand-eye coordinate system transformation

## 4.2 Laser Point Detection

The second part is about detecting the laser point in an image. To make the task simpler, the laser point may only be projected onto a white flip board chart.
Two methods for detecting the laser point are tested.

### 4.2.1 Method 1: HSV Threshold

As lasers are monochromatic one could think about looking for a certain colour. The idea is to define a threshold in HSV-colour space and only look at the pixels that are within this band. By applying a dilation function to the binary image, the weakly connected pixels are morphed together and form blobs. Then the function findCountours is deployed to detect the connected areas of white pixels. Finally, the first (biggest) area contour is taken and the centre of mass is calculated. This is the 2D point in one image.
This method did not work very well. Some problems have been identified:
- Taking the biggest area is not very sensible. More constraints could be helpful like: size threshold, convexity or previous point.
- As the automatic mode of the camera is not deactivated the colour of the laser point might change with different lighting scenarios.
- The definition of the colour threshold is not trivial: Either too many pixels or too few are taken. Especially with a colourful surrounding this trade-off is hard to control.

9

4 Stereo Vision

### 4.2.2 Method 2: Template Matching

The second method uses template matching to find the green laser point. The process outline as follows: a template slides over the image and at every pixel they are compared. The comparison results a scalar value which are then stacked together to create something like a ‘heat-map’. The larger the scalar is at an index, the better is the correspondence between the image and the template.
There are many different methods for comparing two images defined in OpenCV. The utilize method was found to work best for this sort of object detection. The formula is shown in equation 4.2.
The templates are created before every run. In order to make that process as user-friendly as possible, a GUI based configuration app is created. The templates can be seen in the table 4.1.
The main characteristics of this method are:
- This method works much better with different lighting scenarios than the HSV-threshold.
- Motion blurring results in an unstable detection of the laser point. Thus, fast movements with the robot and by hand should be avoided.
- Whenever there is no green laser point in the image, the red laser is detected as green, since this is now the best match.
- This method only works with the background (e.g. white flip board) specified in the template.

R(x, y) =

P
x⁰

,y⁰(T

0
(x

0

, y⁰
) · I

0
(x + x

0
, y + y

0
))
qP
x⁰

,y⁰ T⁰(x

0

, y⁰)
2 ·
P
x⁰

,y⁰ I

0(x + x

0
, y + y

0)
2

(4.2)

Table 4.1: laser point template as created by the configuration app

10

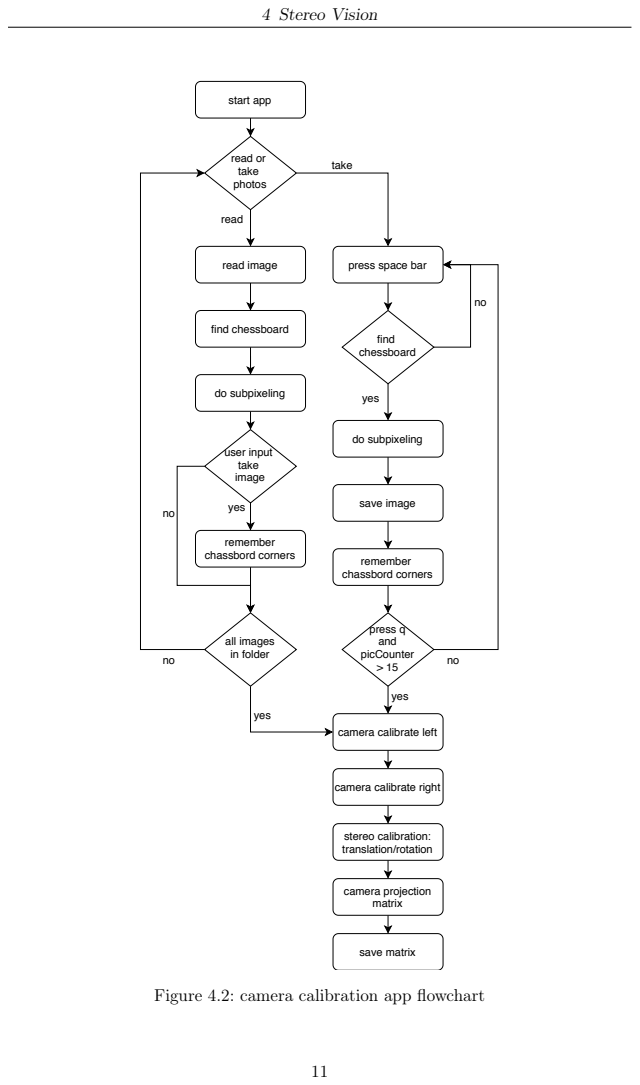
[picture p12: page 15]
4 Stereo Vision; read; yes; find chessboard; do subpixeling; save image; press q and picCounter > 15; remember chassbord corners; read image; remember; all images in folder; yes no; user input take image; stereo calibration: translation/rotation; camera projection matrix; save matrix

start app

take read or
take
photos

press space bar

chassbord corners

camera calibrate left

camera calibrate right

Figure 4.2: camera calibration app flowchart

# 5 Main App

This chapter describes the algorithmic steps taken in the main application as seen in the flowchart 5.1. The action transform 3D point to robot base consists of multiple steps itself:

- Multiply the 3D point with the hand-eye calibration to transform the point into the TCP frame, as seen in 4.1
- Transform the point to the robot base coordinate system by multiplying with the backwards kinematic in 3.1.

12

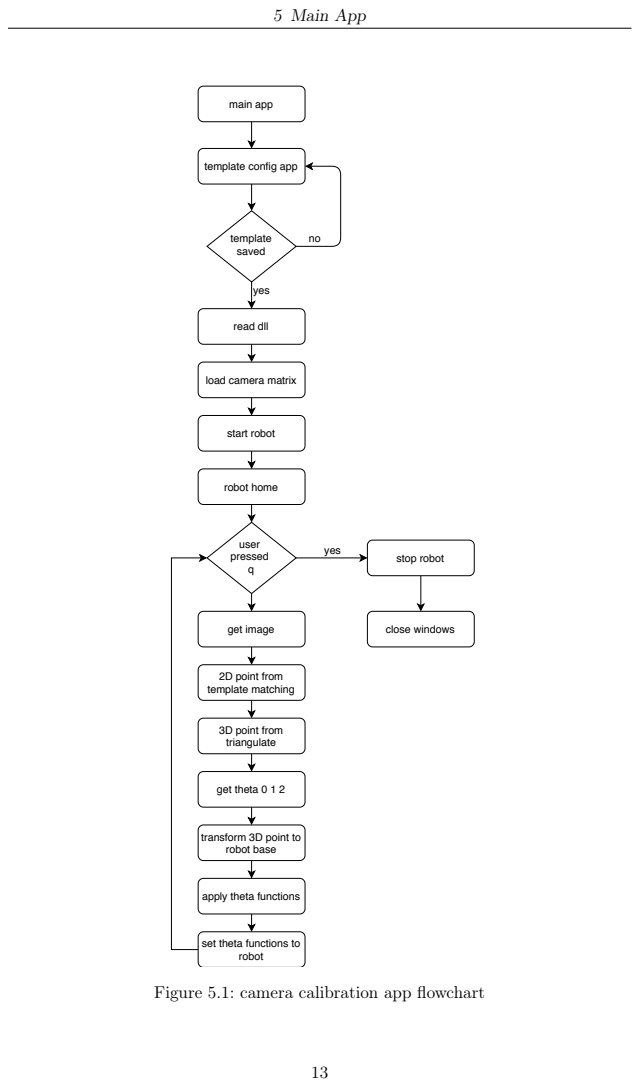
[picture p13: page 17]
5 Main App; main app; read dll; template saved; yes; start robot; robot home; user pressed q; stop robot; close windows; get image; 2D point from template matching; 3D point from triangulate; get theta 0 1 2; robot

template config app

load camera matrix

transform 3D point to
robot base

apply theta functions

set theta functions to

Figure 5.1: camera calibration app flowchart

# 6 Conclusion

We find, that template matching method is better suited to detect small objects in a constantly changing image rather than searching the images for a specific colour.

The resting distance between green and red laser point, as seen in figure 6.1 results from the offset of the laser pointer to the robot tool centre. That can be easily adjusted with a new bracket. To avoid any systematic errors, the laser pointer has to be mounted colinear with the z-axis of the robot tool.

Another current problem is the high energy consumption of the laser pointer. Within a half an hour, the intensity of the laser pointer dropped significantly. In the next step, a more appropriate power supply should be installed.

An additional option could be to specify theta1 as a variable instead of a constant and find a more advanced system of equations.


Figure 6.1: resting offset between laser points

14

# Bibliography

Craig, John (2018): Introduction to Robotics Mechanics and Control (cit. on p. 4).

ROBOTIS-GIT (2019): DynamixelSDK. Robotis Ltd. GitHub. url: github.com/ ROBOTIS-GIT/DynamixelSDK/tree/master/c (cit. on p. 5).

The OpenCV Reference Manual(July 2019). 4.1.1. OpenCV (cit. on p. 8).

15

# Appendices

16

# A Drawings

17

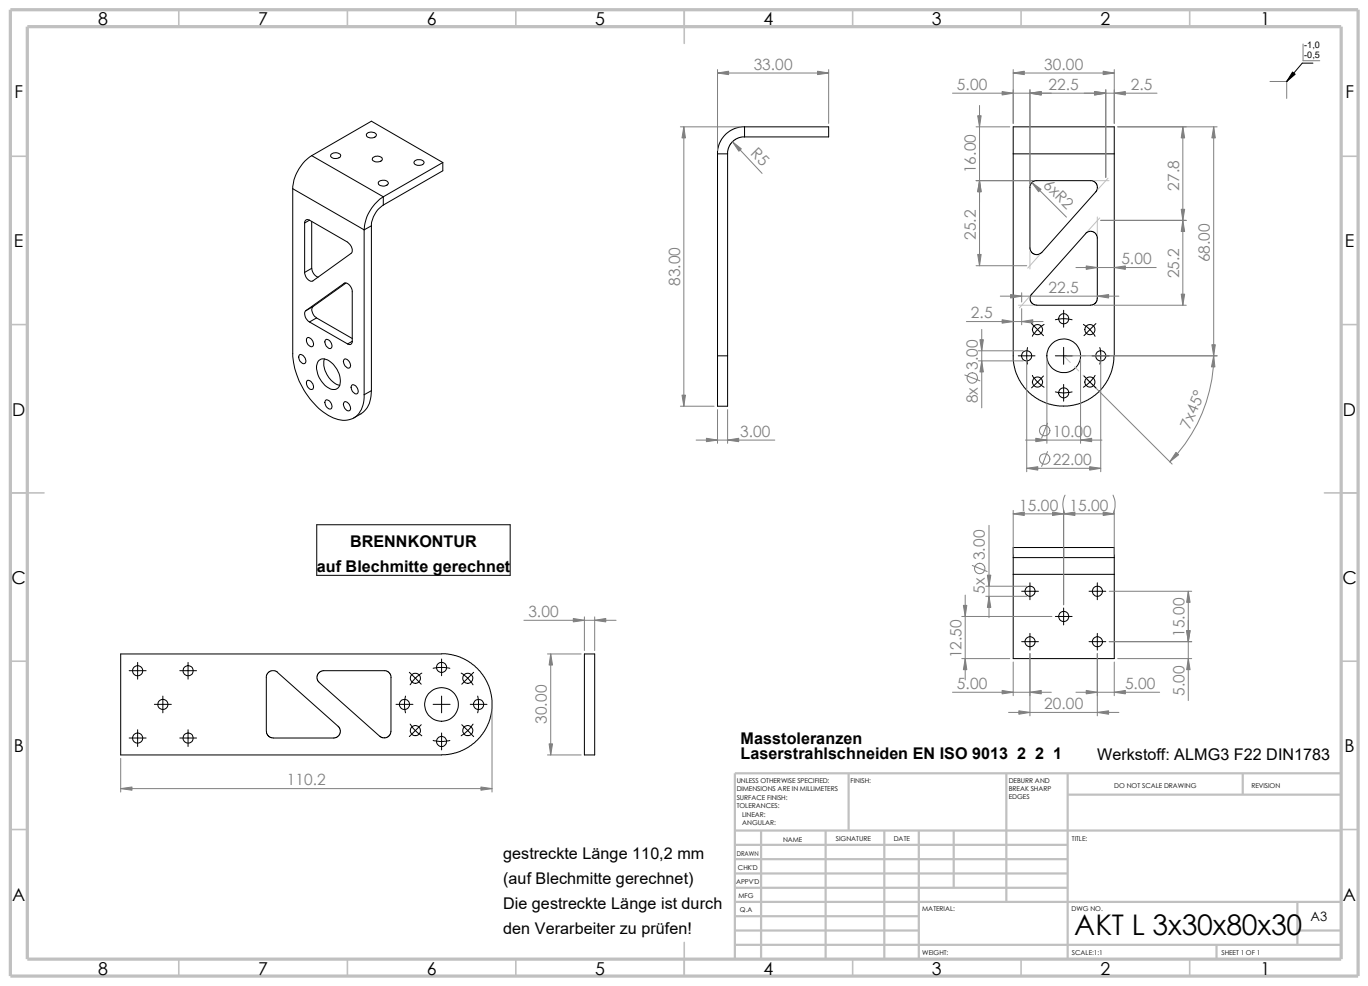
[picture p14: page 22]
SCALE:1:1; SHEET 1 OF 1; WEIGHT:; DO NOT SCALE DRAWING; REVISION; FINISH:; EDGES; DEBURR AND BREAK SHARP; Masstoleranzen; Laserstrahlschneiden EN ISO 9013 2 2 1; Werkstoff: ALMG3 F22 DIN1783

BRENNKONTUR
auf Blechmitte gerechnet

UNLESS OTHERWISE SPECIFIED:
DIMENSIONS ARE IN MILLIMETERS
SURFACE FINISH:
TOLERANCES:
LINEAR:
ANGULAR:

gestreckte Länge 110,2 mm
(auf Blechmitte gerechnet)
Die gestreckte Länge ist durch
den Verarbeiter zu prüfen!

DRAWN
CHK'D
APPV'D
MFG
Q.A | | | | MATERIAL: | DWG NO. AKT L 3x30x80x30 | A3

NAME | SIGNATURE | DATE | | | | TITLE:

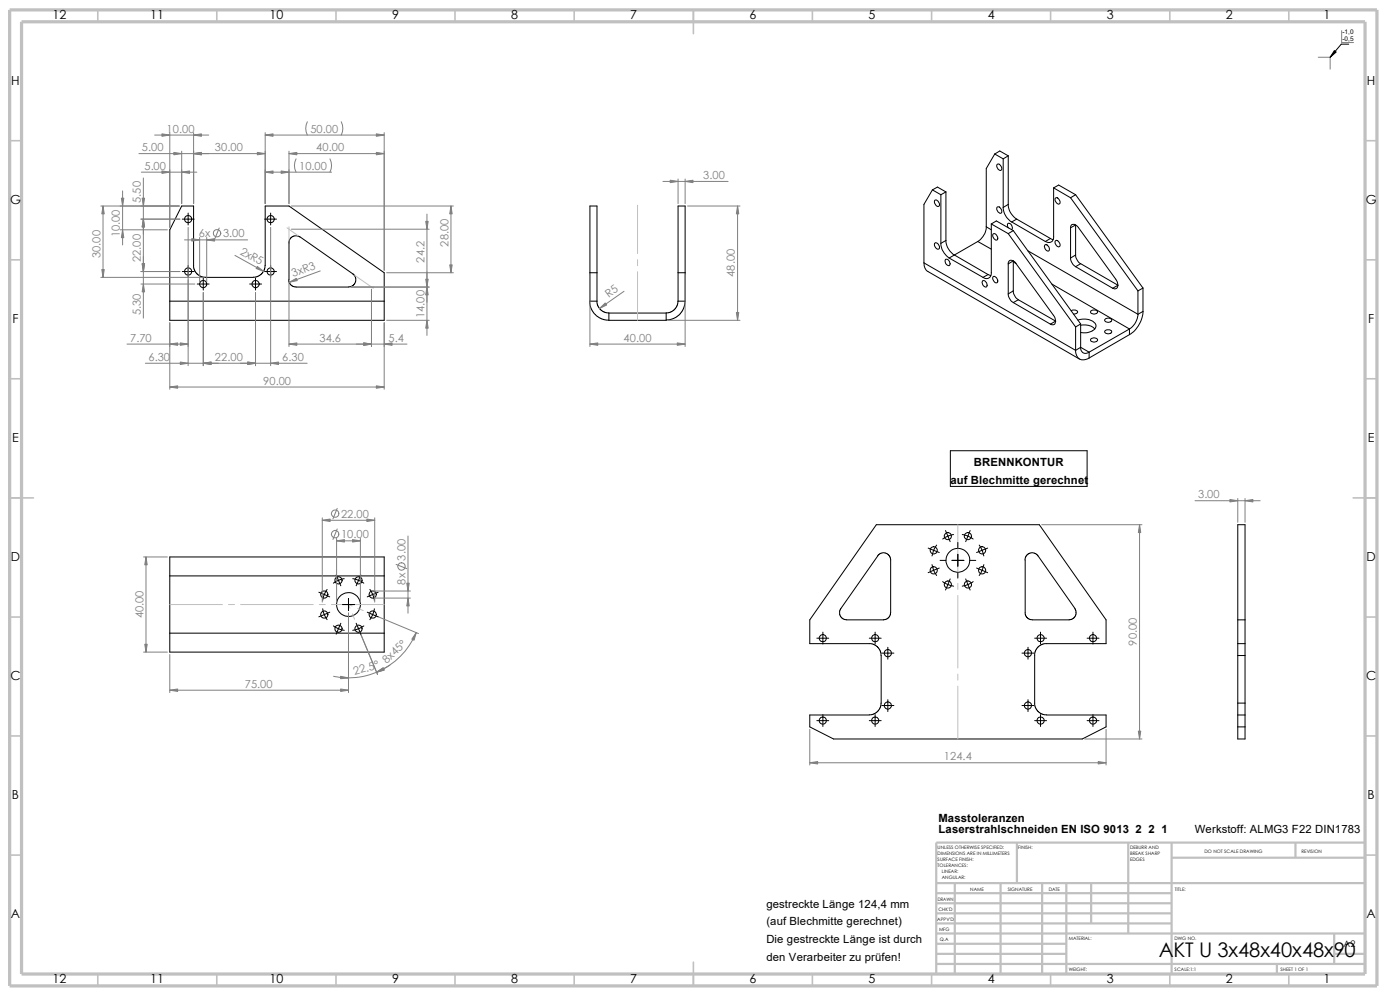
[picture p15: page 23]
DATE; FINISH:; EDGES; NAME; SIGNATURE; DO NOT SCALE DRAWING; REVISION; TITLE:; SCALE:1:1; SHEET 1 OF 1; DEBURR AND BREAK SHARP; Laserstrahlschneiden EN ISO 9013 2 2 1; Werkstoff: ALMG3 F22 DIN1783; Masstoleranzen

BRENNKONTUR
auf Blechmitte gerechnet

UNLESS OTHERWISE SPECIFIED:
DIMENSIONS ARE IN MILLIMETERS
SURFACE FINISH:
TOLERANCES:
LINEAR:
ANGULAR:

gestreckte Länge 124,4 mm
(auf Blechmitte gerechnet)
Die gestreckte Länge ist durch
den Verarbeiter zu prüfen!

MFG | | | | 1 DRAWN
CHK'D
APPV'D

Q.A | WEIGHT: MATERIAL: AKT U 3x48x40x48x90 | DWG NO. | A2

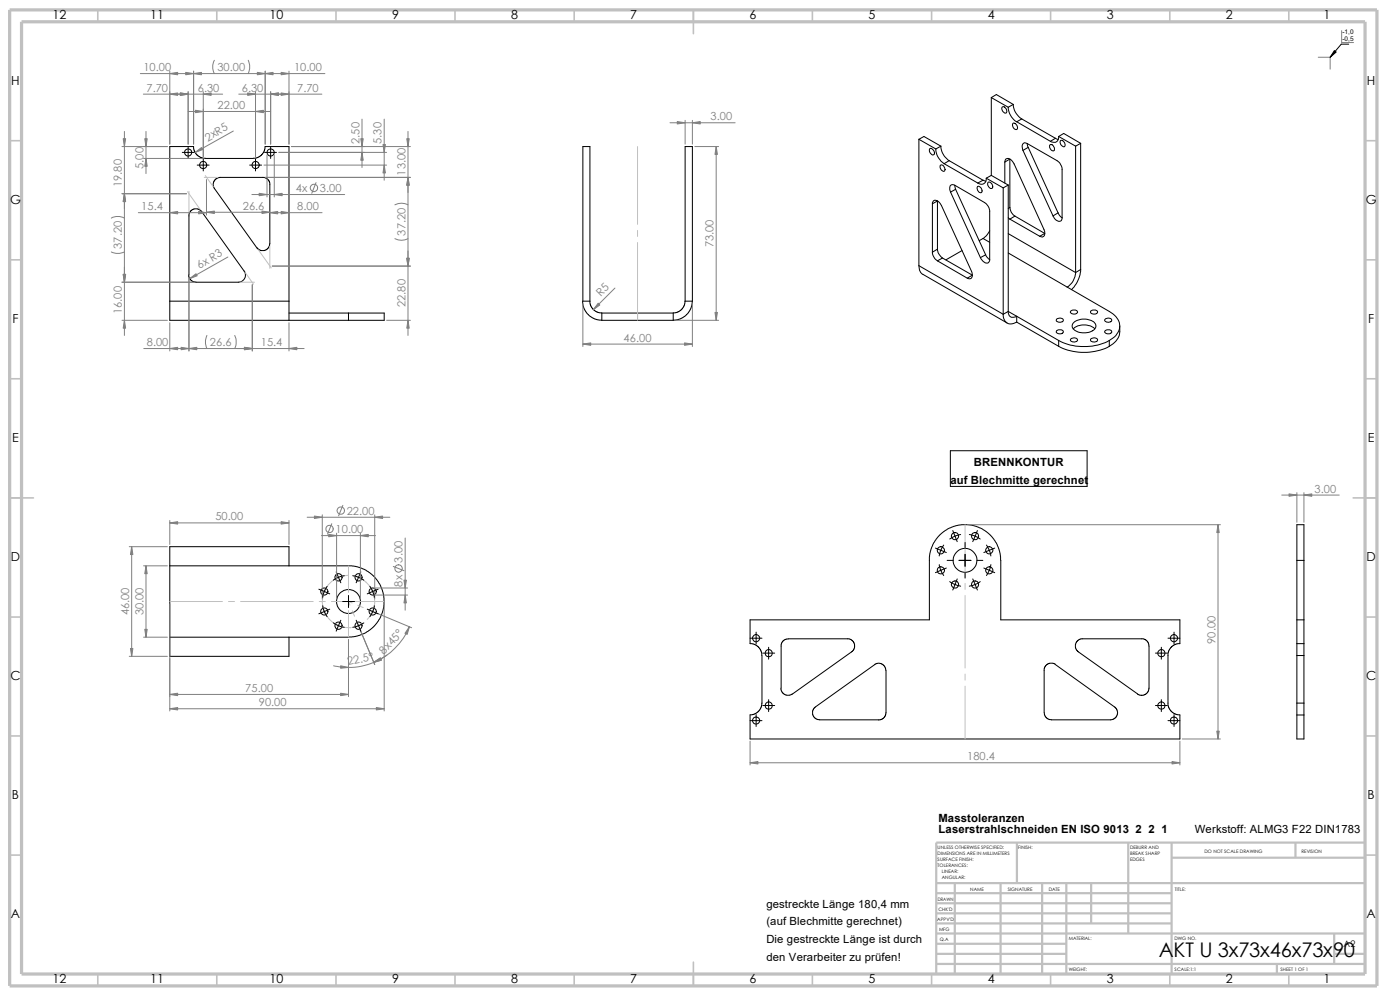
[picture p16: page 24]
SCALE:1:1; FINISH:; EDGES; NAME; SIGNATURE; DATE; REVISION; TITLE:; SHEET 1 OF 1; DEBURR AND BREAK SHARP; Laserstrahlschneiden EN ISO 9013 2 2 1; Werkstoff: ALMG3 F22 DIN1783; Masstoleranzen; (auf Blechmitte gerechnet) ⁵.30

BRENNKONTUR
auf Blechmitte gerechnet

UNLESS OTHERWISE SPECIFIED:
DIMENSIONS ARE IN MILLIMETERS
SURFACE FINISH:
TOLERANCES:
LINEAR:
ANGULAR:

DO NOT SCALE DRAWING

gestreckte Länge 180,4 mm

MFG | | | | 1 DRAWN
CHK'D
APPV'D

Die gestreckte Länge ist durch
den Verarbeiter zu prüfen!

Q.A | WEIGHT: MATERIAL: AKT U 3x73x46x73x90 | DWG NO. | A2

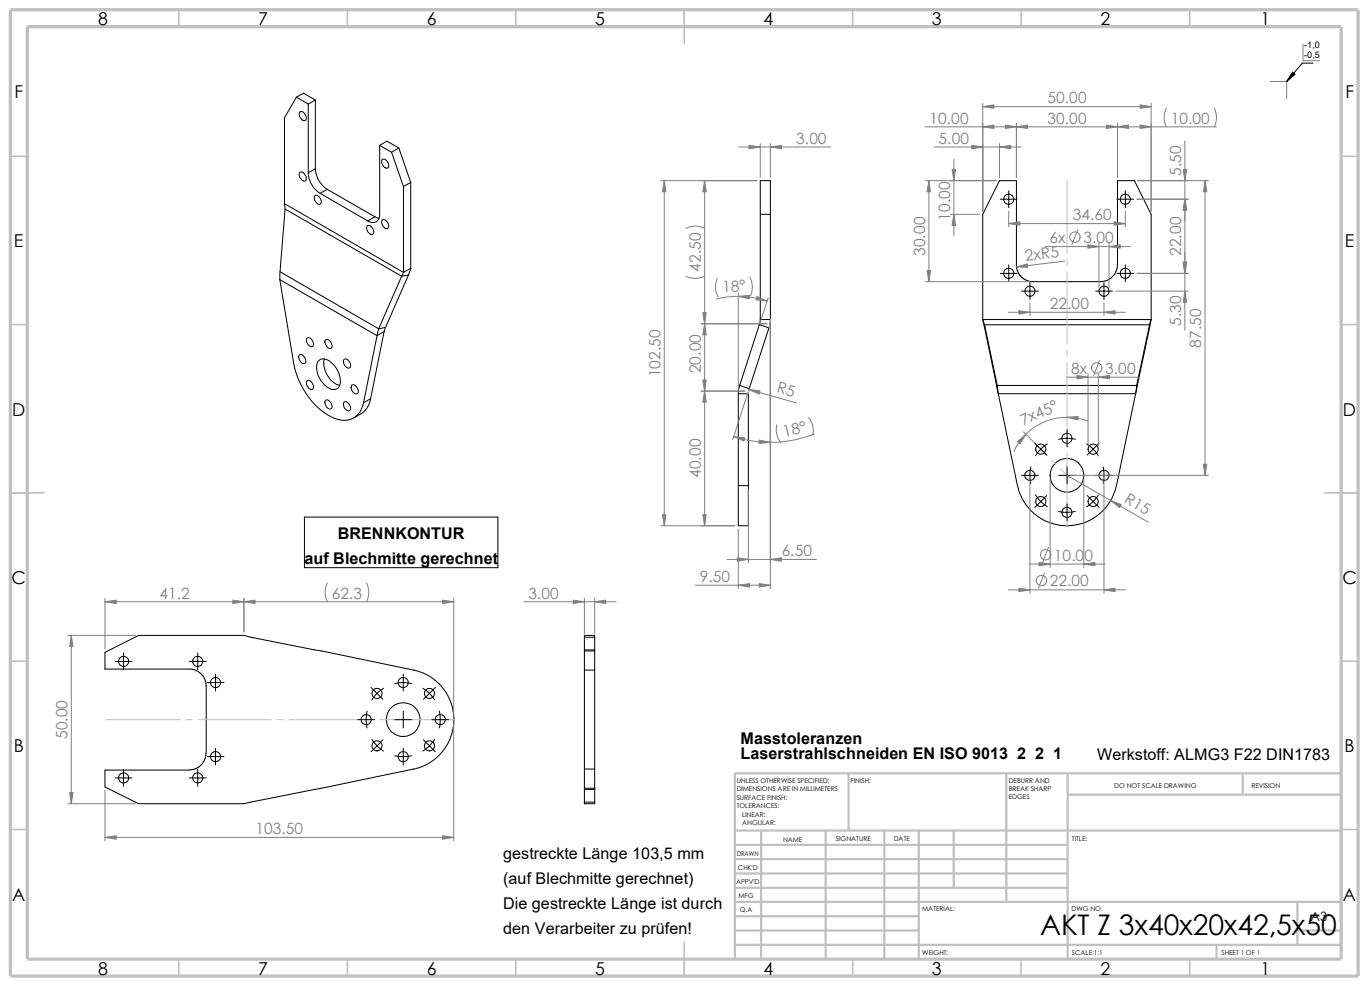
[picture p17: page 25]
SCALE:1:1; SHEET 1 OF 1; WEIGHT:; DO NOT SCALE DRAWING; REVISION; FINISH:; EDGES; DEBURR AND BREAK SHARP; Masstoleranzen; Laserstrahlschneiden EN ISO 9013 2 2 1; Werkstoff: ALMG3 F22 DIN1783; BRENNKONTUR

auf Blechmitte gerechnet 50.00

UNLESS OTHERWISE SPECIFIED:
DIMENSIONS ARE IN MILLIMETERS
SURFACE FINISH:
TOLERANCES:
LINEAR:
ANGULAR:

gestreckte Länge 103,5 mm
(auf Blechmitte gerechnet)
Die gestreckte Länge ist durch
den Verarbeiter zu prüfen!

DRAWN
CHK'D
APPV'D
MFG
Q.A | | | | MATERIAL: AKT Z 3x40x20x42,5x50 | DWG NO. | A3

NAME | SIGNATURE | DATE | | | | TITLE:

# B Motor Parameters

parameter | axis 0 | axis 1 | axis 2
home offset | 2288 | 2060 | 3074
min angle | 1580 | 2060 | 1650
max angle | 3000 | 3200 | 3100
max velocity | 20 | 20 | 20
home | 2290 | 2060 | 3072

Table B.1: table of motor parameters

22

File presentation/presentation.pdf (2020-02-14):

## 3 Axis Robot following a Laserpointer by using Stereovision and Templatematching

Johannes W¨ustner, Nicolai Schwartze

February 6, 2020

jwu, nsc | jeff junior | February 6, 2020 | 1 / 21

1 | Introduction
2 | Design
3 | Calculation
4 | Camera Calibration
5 | Laser Point Detection
6 | Conclusion, Further Work
jwu, nsc | jeff junior | February 6, 2020 | 2 / 21

## Project Description

construct a 3-axis robot with camera/laser tool

calculate the backwards kinematic
program robot functions in C-DLL
calibrate 3D camera system
camera projection matrix
hand-eye calibration
detect laser point on white flip-chart computer vision using OpenCV and Python

drive with red robot laser to green user laser

jwu, nsc | jeff junior | February 6, 2020 | 3 / 21

1 | Introduction
2 | Design
3 | Calculation
4 | Camera Calibration
5 | Laser Point Detection
6 | Conclusion, Further Work
jwu, nsc | jeff junior | February 6, 2020 | 4 / 21

## Task

design a 3-axis robot in SolidWorks

assemble the parts
using Dynamixel MX-64AT motors attach camera/laser tool
jwu, nsc | jeff junior | February 6, 2020 | 5 / 21

## Result

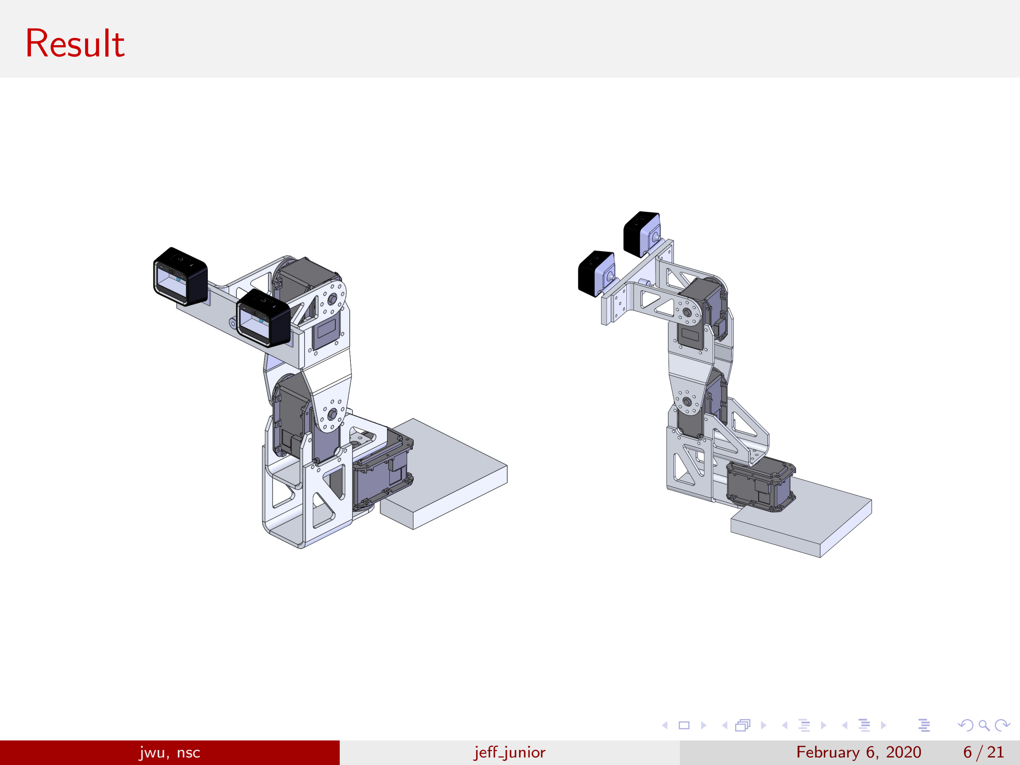
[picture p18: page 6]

jwu, nsc | jeff junior | February 6, 2020 | 6 / 21

1 | Introduction
2 | Design
3 | Calculation
4 | Camera Calibration
5 | Laser Point Detection
6 | Conclusion, Further Work
jwu, nsc | jeff junior | February 6, 2020 | 7 / 21

## Task

generate robot-backwards kinematic
develop equation for setting angle of motor
establish transformation matrix for hand-eye coordination
jwu, nsc | jeff junior | February 6, 2020 | 8 / 21

## Problem

backwards kinematic
establish DH parameter → transformation matrix TCP to robot base setting motor angle
only need two DOF → overdetermined
hand-eye coordination
estimate the right distance camera to TCP
jwu, nsc | jeff junior | February 6, 2020 | 9 / 21

## Solution I

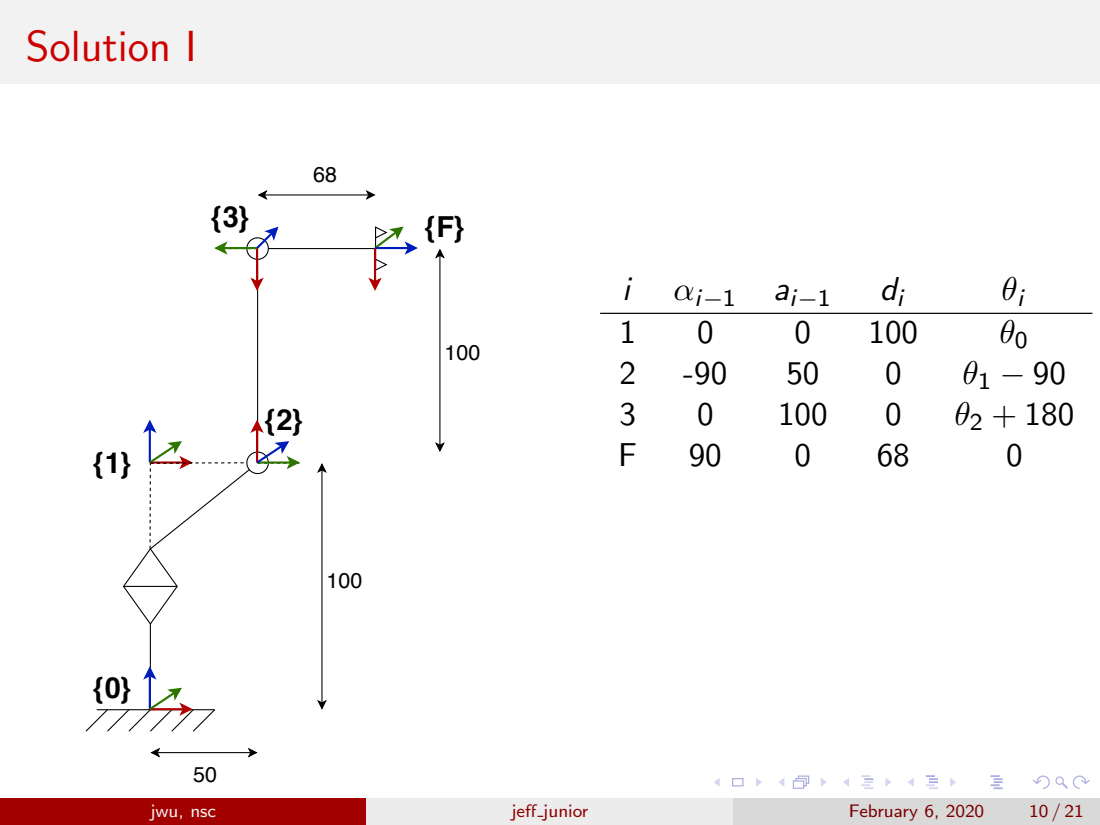
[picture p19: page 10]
jwu, nsc; jeff junior; February 6, 2020

## Solution II

θ0 = arctan(

Y0
X0
) | (1)
θ1 = 0.0 | (2)

θ2 = −1 · arctan

Z0 − 100 − 100cos(θ1)
q
X

2
0 + Y

2
0 − 50 − 100sin(θ1)
- (3)
jwu, nsc | jeff junior | February 6, 2020 | 11 / 21

1 | Introduction
2 | Design
3 | Calculation
4 | Camera Calibration
5 | Laser Point Detection
6 | Conclusion, Further Work
jwu, nsc | jeff junior | February 6, 2020 | 12 / 21

## Task

calculate camera matrix for both single cameras

estimate translation and rotation between cameras

jwu, nsc | jeff junior | February 6, 2020 | 13 / 21

## Problem

unstable against repetition
chessboard must not have the same hight and width three quality control measures:
plausibility: translation vector between cameras measure actual 3D points
comparison with matlab
jwu, nsc | jeff junior | February 6, 2020 | 14 / 21

## Solution

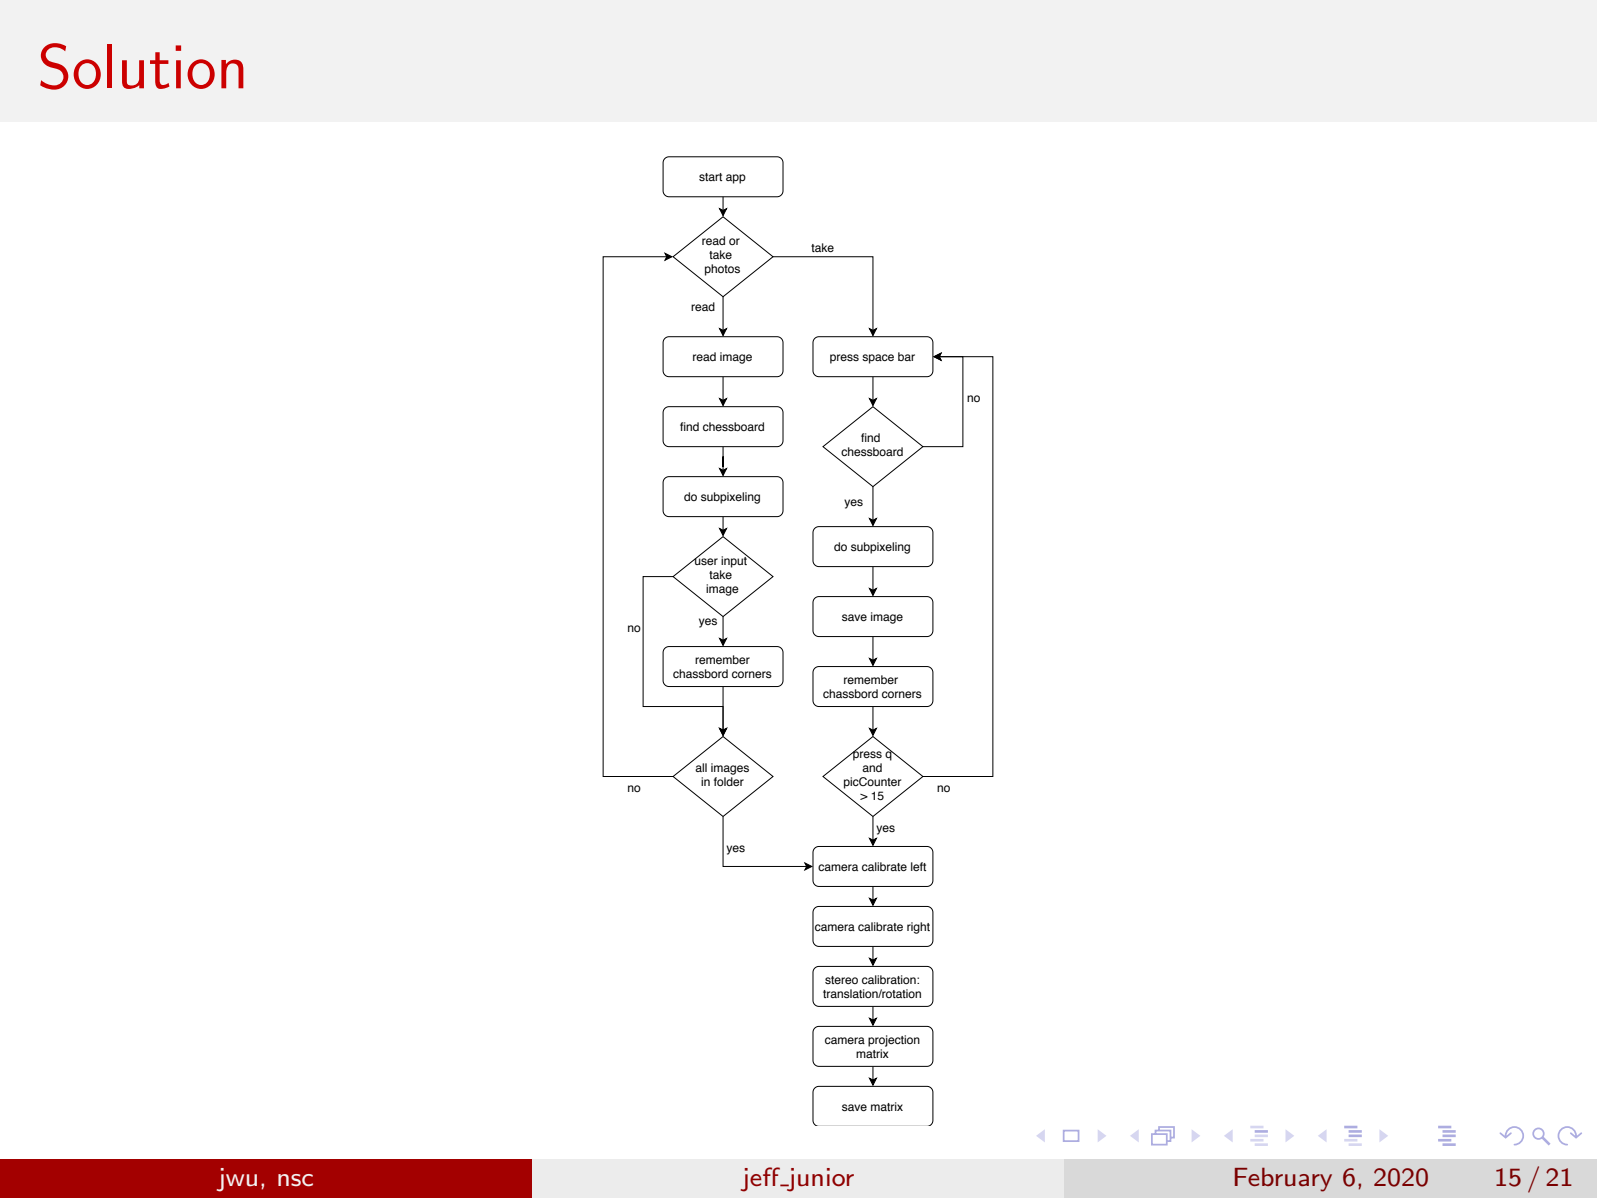
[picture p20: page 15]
start app; read; yes; find chessboard; do subpixeling; save image; press q and picCounter > 15; remember chassbord corners; read image; all images in folder; yes no; user input take image; stereo calibration: translation/rotation; camera projection matrix; save matrix; jwu, nsc; jeff junior; February 6, 2020

take read or
take
photos

press space bar

camera calibrate left

camera calibrate right

1 | Introduction
2 | Design
3 | Calculation
4 | Camera Calibration
5 | Laser Point Detection
6 | Conclusion, Further Work
jwu, nsc | jeff junior | February 6, 2020 | 16 / 21

## Task

detect green laser point
detect red laser point (not used; would be helpful for controller)
jwu, nsc | jeff junior | February 6, 2020 | 17 / 21

## Problem

first idea: use threshold for colour of laser

detect contour
calculate centre of mass

problem: unstable against other lighting conditions

red laser point too small
use laser with adjustable focal length
jwu, nsc | jeff junior | February 6, 2020 | 18 / 21

## Solution

use template matching
created template calibration app before every run

more stable against lighting conditions
but can only work on specified background (like a flip-chart)

using the CV TM CCOEFF NORMED

R(x, y) =

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
) · I

0
(x + x

0
, y + y

0
))
qP
x

0
,y

0 T⁰(x

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
0(x + x

0
, y + y

0)
2

(4)

also works for coloured images, this equation is applied for every channel

jwu, nsc | jeff junior | February 6, 2020 | 19 / 21

1 | Introduction
2 | Design
3 | Calculation
4 | Camera Calibration
5 | Laser Point Detection
6 | Conclusion, Further Work
jwu, nsc | jeff junior | February 6, 2020 | 20 / 21

## Summary, Further Work

works (sort of) but slow convergence

overshooting
resting offset
not using θ1
3 USB ports needed - opencv does not find camera on hub red laser uses loads of batteries 220mAh
45mA = 4.8h

implement controller
correct laser offset to align with axis θ2 use undistort before calculateing 3D point power supply for laser
jwu, nsc | jeff junior | February 6, 2020 | 21 / 21

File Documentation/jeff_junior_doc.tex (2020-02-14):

%
% 1: documentation, e.g.: a documentation for a project done in a course
% 2: thesis, e.g.: a master thesis
% 3: summary
% 5: presentation
% 9: paper
%
\ifx\FHVmode\undefined
	\def\FHVmode{1}
\fi
%
% 1: Presentation only
% 2: Presentation only notes
% 3: Presentation all (left page is the presentation, right the notes)
%
\ifx\PresentationMode\undefined
	\def\PresentationMode{3}
\fi
%
\def\paperStyle{fhv}
%
\newcommand{\version}{v0.0}
%
\pdfminorversion=7 % use newer pdf version
\pdfobjcompresslevel=2
\pdfsuppresswarningpagegroup=1
%
\input{./sty/overallDefines.sty}
%
\documentclass[\documentclassOptions]{\komaScriptClass}
%
\usepackage{./sty/fhv}
%
\makeglossaries
\renewcommand{\glsnamefont}[1]{\textbf{#1}}
%
% General Settings for Title...
%
\setLanguage{\newLanguage}
\setTitle{Jeff Junior}
\setThesistype{Project Documentation}
\setAuthor{\authorSurname\authorName}
\setAuthorId{MATRIKELNUMMER}
\setStudyprogram{Master's in Mechatronics}
\setSupervisor{\supervisorSurname\supervisorName}
\setSupervisorCompany{Title B SupervisorCompanyName, Title A}
\setSubtitle{3 Axis Robot following a Laserpointer by using Stereovision and Templatematching}
\setSubject{Applied Robotics}
\setDegree{Master of Science in Engineering, MSc}
\setCompany{Company Name GmbH}
%
% PDF Settings
%
\pdfSettings
%
\allowdisplaybreaks
%
% hack to get the caption wider for a table
%
\renewcommand{\TPTminimum}{\linewidth}
%
\begin{document}
	%
	% Select the language defined in \newLanguage
	%
	\ifx\newLanguage\ngerman
		\selectlanguage{ngerman}
	\else
		\selectlanguage{english}
	\fi %
	%
	\if\FHVmode\paper
		\SetAlgorithmName{Algorithmus}{Alg.}
	\makeatletter
		\crefname{equation}{Gl.}{Gln.}
	\makeatother
	\fi
	% Import the acronyms
	%
	\input{./util/Acronym.tex} % provide the defined acronyms to be used
	%
	% for Backlinks to work properly
	%
	%
	\begin{envModeNot}[\presentations]
		%
		% for Backlinks to work properly
		%
		\let\hypercontentsline=\contentsline
		\renewcommand{\contentsline}[4]{\hypertarget{toc.#4}{}\hypercontentsline{#1}{#2}{#3}{#4}}%
		%
		\sisetup{output-decimal-marker = {,}}
		\pagenumbering{gobble} % used to prevent the page numbering
		%
		\begin{envDebug}
			\layout
			\textrm{Serif: \rmdefault}\par
			\textsf{Sans-Serif: \sfdefault}\par
			\texttt{Teletype: \ttdefault}
		\end{envDebug}
		%
		\begin{envModeNot}[\paper]
		%
		% evtl. Sperrvermerkseite
		% nur in begründeten Ausnahmefällen verwenden
		% Aufgrund gesetzlicher Bestimmungen ist eine Sperre maximal für fünf Jahre möglich
		%
		\sperrvermerk{5}
		%
		\end{envModeNot}
		%
		\maketitle % creates the title page
		\hypersetup{pageanchor=true}
		%
		\begin{envModeNot}[\paper]
		%
		\pagenumbering{Roman} 
		%
		%\subfile{./tex/Abstract.tex}
		\newpage
		%
		\fhvlists
		\end{envModeNot}
		%
		% INSERT your .tex files
		%
		\subfile{./tex/MainPart.tex}
		%\subfile{./tex/xxx.tex}
		%\subfile{./tex/Examples.tex}
		%
		% END INSERT
		%
		\glossaryAndBibliography
		%
		% uncomment this if you like a short CV
		% \subfile{./tex/Lebenslauf.tex}
		%
		\begin{envModeNot}[\paper]
			\newpage
			\appendix
			\addAppendix{
			%
			% INSERT your .tex files
			%
			\subfile{./tex/Anhang.tex}
			%
			% END
			%
			}
			% Statuory Declaration
			\statuoryDeclaration
			%
		\end{envModeNot}
	\end{envModeNot}
	%
\end{document}

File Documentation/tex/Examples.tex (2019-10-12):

\documentclass[./\jobname.tex]{subfiles}
\begin{document}
%

%
\if\paper\FHVmode
	\section{Mathemodus}
\else
	\chapter{Mathemodus}
\fi
%
\begin{align}
\text{det}(\lambda \cdot \mathds{1} -A) &= 0 \underbrace{\longrightarrow}_{\substack{\text{Zustands-} \\ \text{rückführung}}} \text{det}\left[\lambda\cdot \mathds{1} - \left(A-b\cdot k\right)\right]=0\label{eq: eigenwerte rueckfuehrung}\\
\sin(x)^{2} + \cos(x)^{2} &= 1\label{eq: cos sin}
\end{align}
%
Ich bin eine super Referenzierung: \cref{eq: eigenwerte rueckfuehrung}. Oder noch besser wenn auf mehrere Gleichungen referenziert werden will: \cref{eq: eigenwerte rueckfuehrung,eq: cos sin}.
%
\if\paper\FHVmode
	\section{BiB \& Acronyme}
\else
	\chapter{BiB \& Acronyme}
\fi
%
\begin{itemize}
	\item Dies ist eine Qullenangabe: \parencite[Vgl.][S.220-224]{IEEE802.1Q2014}.
	\item Dies ist eine \gls{cbs}.
	\item Zweite Verwendung von einem Acronym: \gls{cbs}.
	\item Dies ist eine Fußzeile\footnote{Das ISO/OSI Model kann in \cite[][S.2-9]{Mandl2010} nachgeschlagen werden.}.
	\item \textcite[][S.2-9]{Mandl2010} nachgeschlagen werden.
	\item \parencite{Gibb1965Light} für Herausgeberwerke.
\end{itemize}
%
\begin{figure}
	\centering
	\rule{1cm}{1cm}
	\unterschrift{\citeauthor{Mandl2010}}{}{}
\end{figure}
%
So kann direkt Zitiert werden:
%
\begin{quote}
	\enquote{\textit{ich bin ein direktes Zitat}} \cite{Broster2001}
\end{quote}
%
Acronym Tests: \enquote{ \glspl{fpsLabel} \glspl{fpsLabel}} für Plural.
%
\newpage
%
\gls{tsn} \gls{jtag} \gls{sram} \gls{slam} \gls{bluecom} \gls{bluecom} \gls{profinet} \gls{ptp} \gls{bmca} \gls{dns} \gls{fpga} \gls{ack} \gls{bb} \gls{raspy} \gls{can} \gls{adc} \glspl{wlan} \gls{fft} \gls{fpu} \gls{bpsk} \gls{cgi}\par
%
\blindtext[1]
%
\if\paper\FHVmode
	\section{Bilder}
\else
	\chapter{Bilder}
\fi
%
In \autoref{fig: example-image} ist ein Beispiel einer Abbildung dargestellt.
%
\begin{figure}[H]
\centering
\noindent\adjustbox{max width=\linewidth}{% if the picture is greater than \textwidth, it is going to be resized to \textwidth.
	% trim option's parameter order: left bottom right top
	
}
	% if you don't have to print the source, just remove it e.g.:
	%\unterschrift{ich bin die Unterschrift}{}{}
	% if you don't want to have your caption in the table of contents use the #3 argument to prevent the listing in the table of contents. e.q.:
	%\unterschrift{ich bin die Unterschrift}{Quelle}{no}
	\unterschrift{ich bin die Unterschrift}{Quelle}{}
	\label{fig: example-image}
\end{figure}
%
In \Cref{fig: Bild A,fig: Bild A} (oder mit Abkürzung \cref{fig: Bild A,fig: Bild A}) ist ein Beispiel einer Abbildung mit zwei Bildern dargestellt. \autoref{fig: Bild A und B} referenziert wiederum auf beide Bilder.
%
\begin{figure}[H]
	\centering
	\begin{subfigure}[b]{0.5\linewidth}
		\centering
		
		\caption{Bild A}
		\label{fig: Bild A}
	\end{subfigure}% 
	%
	\begin{subfigure}[b]{0.5\linewidth}
		\centering
		
		\caption{Bild B}
		\label{fig: Bild B}
	\end{subfigure}%
	\unterschrift{Bildunterschrift für beide Bilder}{\cite{Dorner2010}}{}%
	\label{fig: Bild A und B}
\end{figure}
%
\if\paper\FHVmode
	\subsection{Spezial}
\else
	\section{Spezial}
\fi
%
\def\spaceX{1.5}
\begin{figure}[H]
	\centering
	\noindent\adjustbox{max width=\linewidth}{
\begin{tikzpicture}%[scale=0.7]
\begin{scope}[every node/.style={bgelement}]
\node (Se) at (0,0) {Se};
\node[right=\spaceX of Se] (i) {1};
\node[above=\spaceX of i] (Iel) {$I:L_{a}$};
\node[below=\spaceX of i] (Rel) {$R:R_{a}$};
\node[right=\spaceX of i,label=below:{$\varPsi=k_{m}$}] (GY) {GY};
\node[right=\spaceX of GY] (w) {1};
\node[above=\spaceX of w] (Im) {$I:J_{m}$};
\node[below=\spaceX of w] (Rm) {$R:b_{m}$};
\end{scope}
\draw[bonds]
(Se) edge [e_out,effort={$U$}, flow={$i_a$}] (i)
(i) edge [e_out,effort={$U_{La}$}, flow={$i_a$}] (Iel)
edge [e_in,effort={$U_{Ra}$}, flow={$i_a$}] (Rel)
edge [e_in,effort={$U_{emf}$}, flow={$i_a$}] (GY)
(GY) edge [e_out,effort={$T$}, flow={$\omega$}] (w)
(w) edge [e_out,effort={$T_{j}$}, flow={$\omega$}] (Im)
edge [e_in,effort={$T_{b}$}, flow={$\omega$}] (Rm);
\end{tikzpicture}
}
	\unterschrift{Kausalisierter Bondgraph}{eigene Ausarbeitung}{}
\label{fig: kausalisierter bondgraph}
\end{figure}
%
\def\bildA{true}
\begin{figure}[H]
	\centering
	\noindent\adjustbox{max width=\linewidth}{%
	\subfile{./img/tikz/escon-schaltplan.tex}
}
	\unterschrift{Schaltkreis: Escon 50/5 Controller für Polverschiebung}{eigene Ausarbeitung}{}
	\label{fig: Schalplan Polverschiebung}
\end{figure}
%
\def\bildA{true}
\begin{figure}[H]
	\centering
	\noindent\adjustbox{max width=\linewidth}{%
		\subfile{./img/tikz/blockschaltbild-state-space.tex}
	}
	\unterschrift{Zustandsregler mit Rückkopplungsverstärkungsmatrix f}{eigene Ausarbeitung}{}
	\label{fig: blockschaltbild-state-space.tex A}
\end{figure}
%
\if\paper\FHVmode
	\section{Tabellen}
\else
	\chapter{Tabellen}
\fi
%
\begin{table}[H]
	\centering
	\noindent\adjustbox{max width=\linewidth}{
		\begin{tabular}{|c|c|c|c|c|c|c|c|c|c|}
			\hline
			\rowcolor[HTML]{\farbeTabA}
			Switch Typ & load & $n$ & min & max & $\tilde{x}$ & $\bar{x}$ & $\sigma^{2}$ & $\sigma$ \\ \hline
			Akro 6/0 & nein & 1199602 & 145.12 & 151.32 & 147.92 & 147.91 & 1.12 & 1.06	\\ \hline
			\rowcolor[HTML]{\farbeTabB} 
			Akro 6/0 & ja & 1199382 & 145.12 & 151.40 & 147.88 & 147.89 & 1.13 & 1.06 \\ \hline
		\end{tabular}
	}
	\unterschrift{Tabellen Unterschrift}{eigene Ausarbeitung}{}
	\label{tab: Tabelle A}
\end{table}
%
% Table with footnotes
%
\begin{table}[H]
	\centering
	\begin{threeparttable}
		\makebox[\linewidth]{%
			\begin{tabular}{c|p{5cm}}
				\hline
				\textbf{Typ} & \textbf{Eigenschaften}                                                                                                                                                                                                                                      \\ \hline
				Table 2 & \enquote{Fußnote}\tnote{a}\\\hline
				Table 2 & Fußnote\mtnote{b}\\\hline
				
			\end{tabular}}
		\unterschrift{Fußnoten in einer Tabelle}{eigene Ausarbeitun}{}
		\label{tab: Tabelle B}
		%
		\begin{tablenotes}
			\item [a] Diese Fußnote mit \enquote{\(\backslash\)tnote} nach \enquote{\(\backslash\)enquote} Umgebung verwenden
			\item [b] Ich bin die Fußnote zu b, für normalen Text.
		\end{tablenotes}
	\end{threeparttable}
	%
\end{table}
%
\if\paper\FHVmode
	\section{Listing}
\else
	\chapter{Listing}
\fi
%
\begin{lstlisting}[caption={example}]
for i:=maxint to 0 do
begin
	{ comment } %(*\label{comment a}*)
end;
for i:=maxint to 0 do
begin
{ comment } %(*\label{comment b}*)
end;
for i:=maxint to 0 do
begin
{ comment } %(*\label{comment c}*)
end;
\end{lstlisting}
%
\begin{lstlisting}[caption={example}]
for i:=maxint to 0 do
begin
{ comment } 
end;
for i:=maxint to 0 do
begin
{ comment }
end;
for i:=maxint to 0 do
begin
{ comment }
end;
\end{lstlisting}
%
Line \ref{comment a} shows a comment. Die Escape Operatoren können unter \enquote{./sty/Listings.sty} geändert werden. 
%
\if\paper\FHVmode
	\section{Todo List}
\else
	\chapter{Todo List}
\fi
%
\lipsum[1] 
\todo{This is a to do note at margin}
\lipsum[2] 
\todo[inline]{This is a todo note inline} 
\lipsum[3]
%
\if\paper\FHVmode
	\section{SVG Beispiel}
\else
	\chapter{SVG Beispiel}
\fi
%
\begin{enumerate}
	\item Installiere Inkscape
	\item Als erstes muss unter \enquote{Tools} \pfeil \enquote{Benutzer} \pfeil \enquote{SVG to PDF} die Konvertierung von SVG zu PDF gestartet werden. Dies sucht alle \enquote{.SVG} Dateien und wandelt diese zu \enquote{.PDF} Dateien um mit einer zusätzlichen Endung \enquote{-svg-raw.pdf}.\label{schritt translate}
	\item Anschließend kann das Dokument normal Übersetzt werden.
	\item Sind Änderungen an den SVG Dateien gemacht worden so muss \ref{schritt translate} ausgeführt werden.
\end{enumerate}
%
\begin{figure}[H]
	\centering
	
	\unterschrift{Beispiel für SVG}{eigene Ausarbeitung}{}
	\label{fig: beispiel svg}
\end{figure}
%
\if\paper\FHVmode
	\section{Algorithmen}
\else
	\chapter{Algorithmen}
\fi
%
Der \autoref{algo: first algo} ist gut.\par
%
\begin{algorithm}
	\SetAlgoNoLine
	\DontPrintSemicolon
	\KwData{this text}
	\KwResult{how to write algorithm with \LaTeX2e }
	initialization\;
	\While{not at end of this document}{
		read current\;
		\eIf{understand}{
			go to next section\;
			current section becomes this one\;
		}{
			go back to the beginning of current section\;
		}
	}
	\unterschrift{How to write algorithms}{\url{https://en.wikibooks.org/wiki/LaTeX/Algorithms}}{}
	\label{algo: first algo}
\end{algorithm}
%
\begin{algorithm}
	\SetAlgoNoLine
	\DontPrintSemicolon
	\KwData{this text}
	\KwResult{how to write algorithm with \LaTeX2e }
	initialization\;
	\While{not at end of this document}{
		read current\;
		\eIf{understand}{
			go to next section\;
			current section becomes this one\;
		}{
			go back to the beginning of current section\;
		}
	}
	\unterschrift{How to write algorithms}{\url{https://en.wikibooks.org/wiki/LaTeX/Algorithms}}{}
	\label{algo: second algo}
\end{algorithm}
%
\if\paper\FHVmode
	\section{Referenzieren in den Anhang}
\else
	\chapter{Referenzieren in den Anhang}
\fi
%
\if\paper\FHVmode
	\subsection{test}
\else
	\section{test}
	\autoref{sec: test anhang}
\fi
%
\end{document}

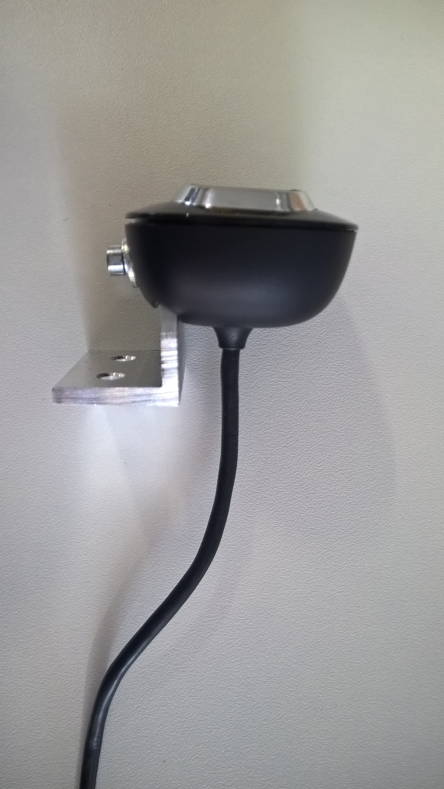
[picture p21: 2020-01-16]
design/images/camera_with_mount.jpg

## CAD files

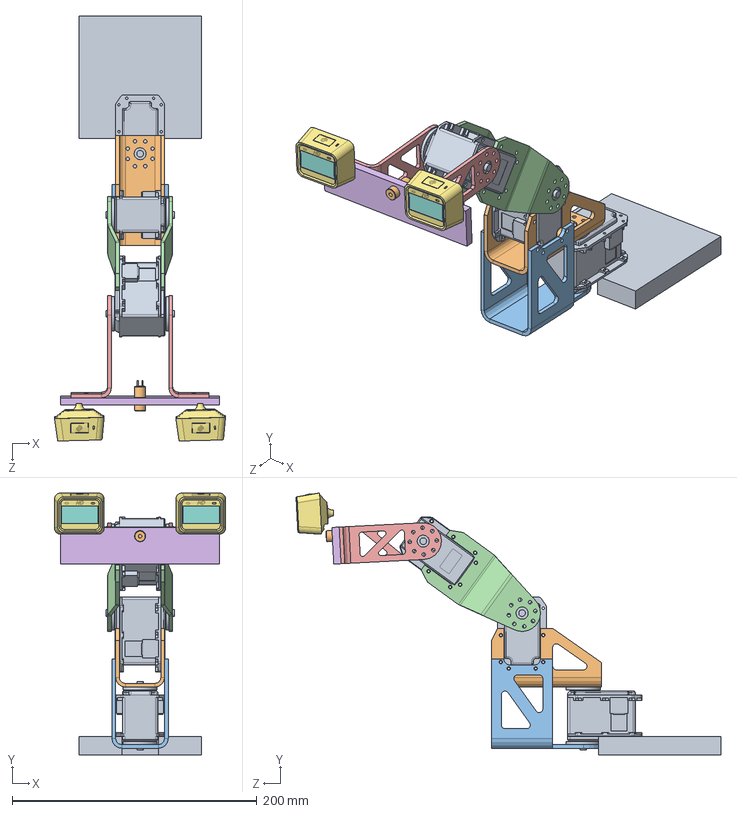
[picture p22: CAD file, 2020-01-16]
design/SWX_model/3AchsRoboter.SLDASM
139.9 x 214.2 x 347.3 mm
MX-64AT_AR x 3
AKT U 3x48x40x48x90
AKT U 3x73x46x73x90
AKT Z 3x40x20x42,5x50 x 2
AKT L 3x30x80x30 x 2
AKT U 1_copy_copy_copy_copy
User Library-Microsoft HD-5000 Web Camera_Camera Body x 2
User Library-Microsoft HD-5000 Web Camera_Glass x 2
AKT U 1_copy_copy_copy_copy_copy
Lasermodul_LFD650

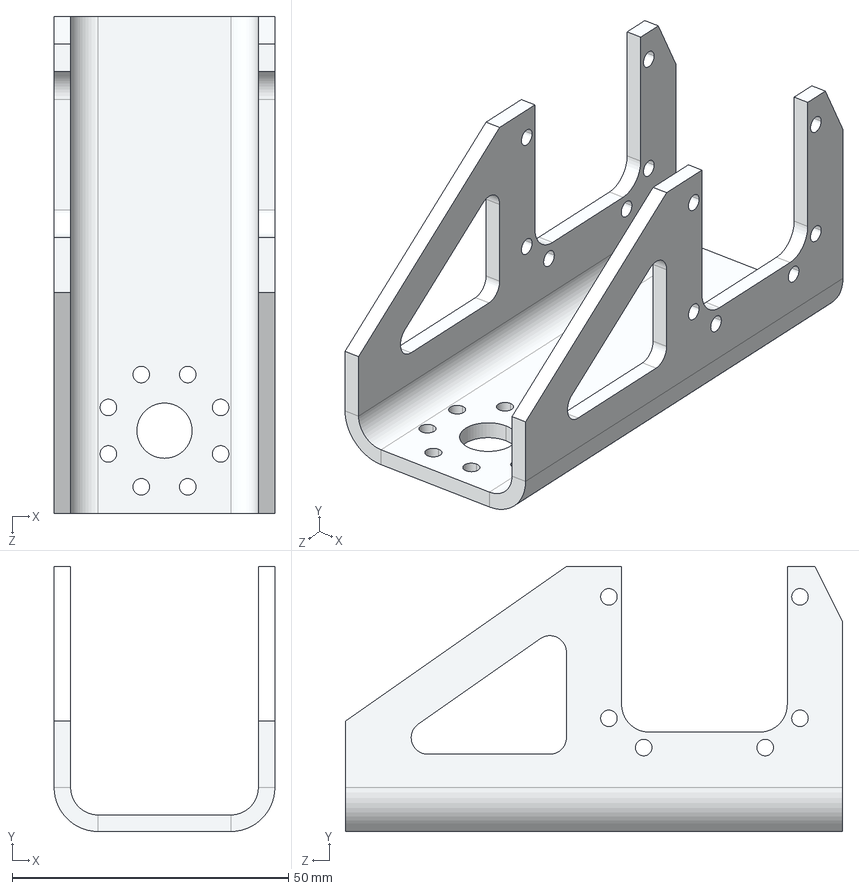
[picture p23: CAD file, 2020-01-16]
design/drawings/AKT U 3x48x40x48x90.STEP
40.0 x 48.0 x 90.0 mm

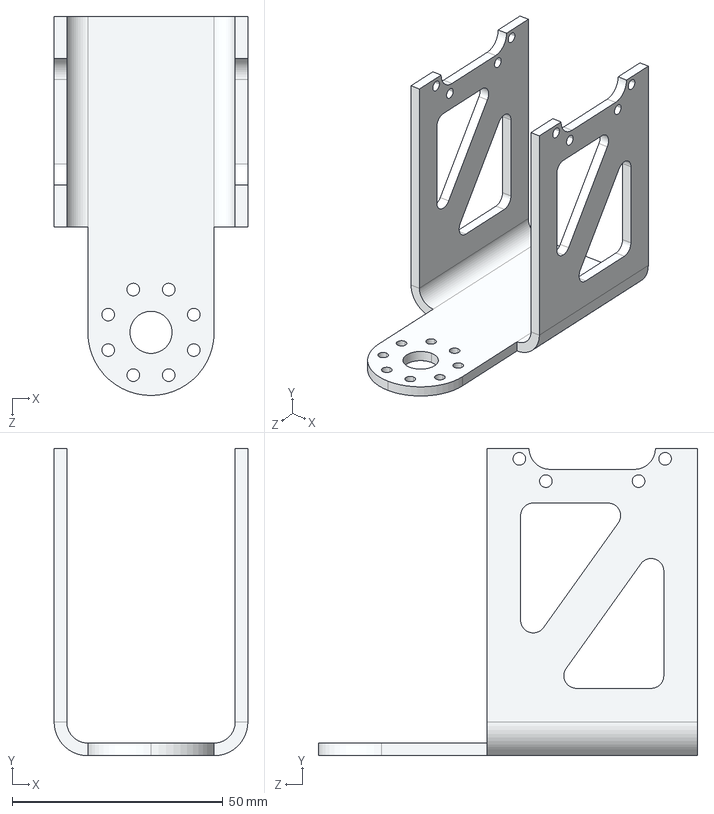
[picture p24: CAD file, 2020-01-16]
design/drawings/AKT U 3x73x46x73x90.STEP
46.0 x 73.0 x 90.0 mm

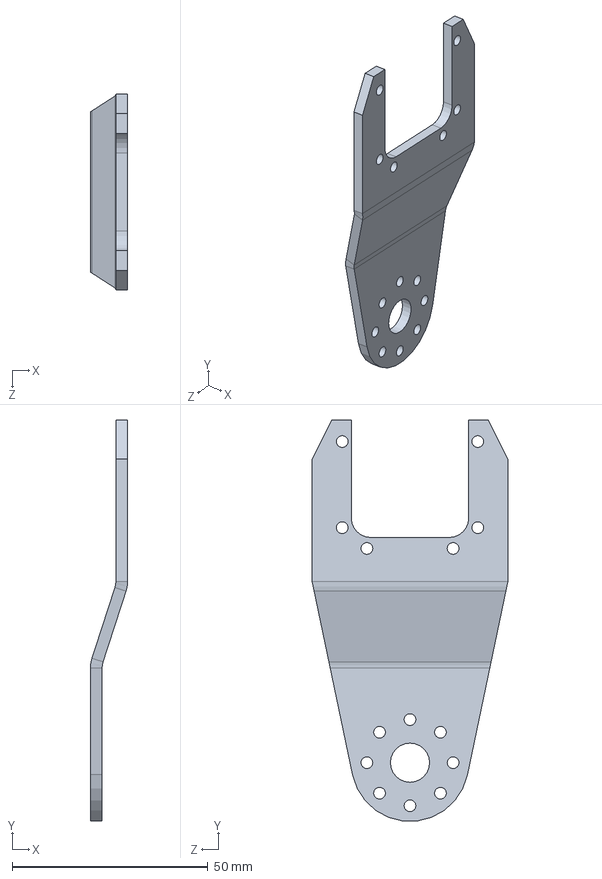
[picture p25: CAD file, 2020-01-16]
design/SWX_model/AKT Z 3x40x20x42,5x50.SLDPRT
9.50 x 102.4 x 50.0 mm

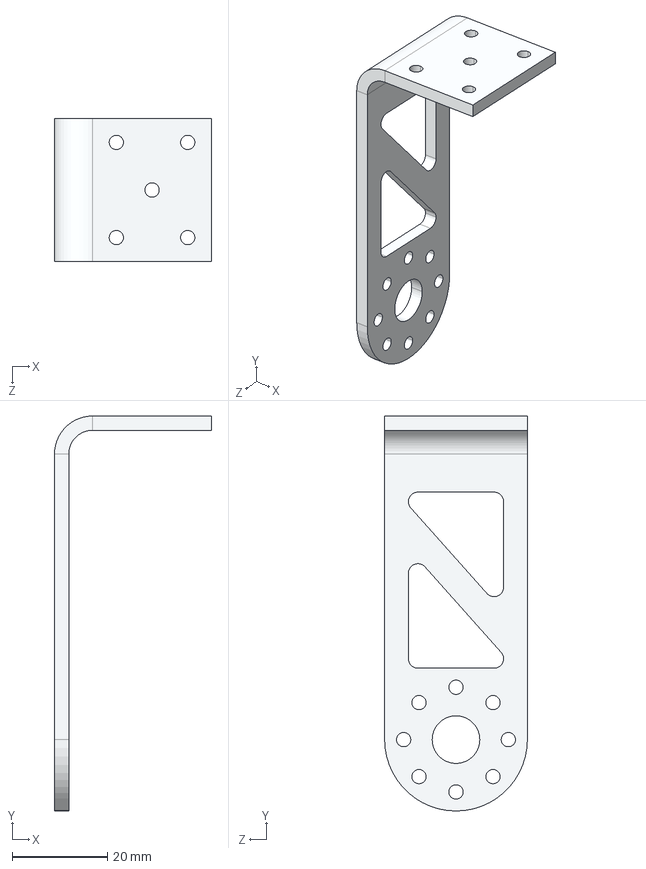
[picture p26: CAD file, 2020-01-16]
design/drawings/AKT L 3x30x80x30.STEP
33.0 x 83.0 x 30.0 mm

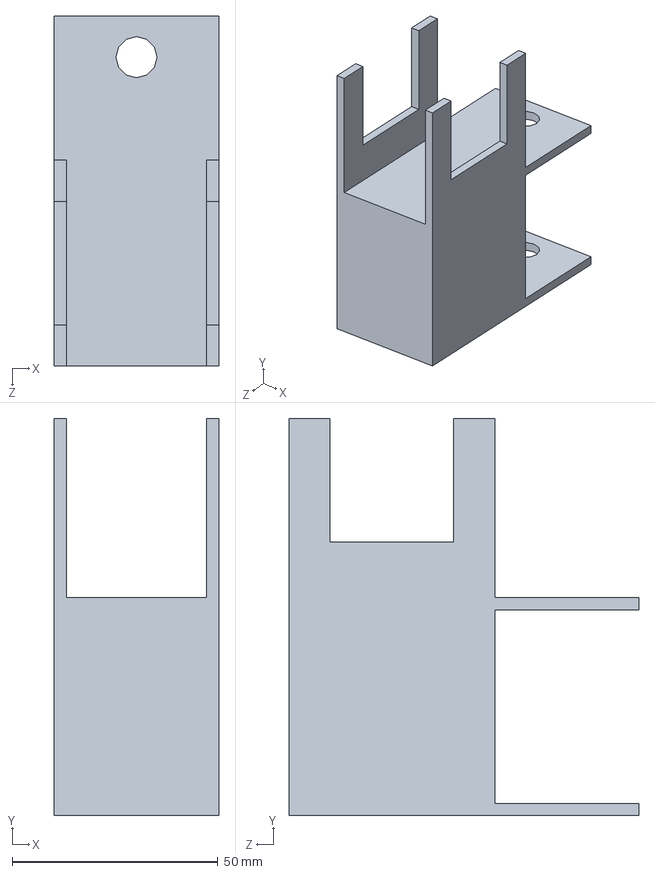
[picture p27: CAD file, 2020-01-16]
design/SWX_model/Hilfsteil.SLDPRT
40.0 x 96.5 x 85.0 mm

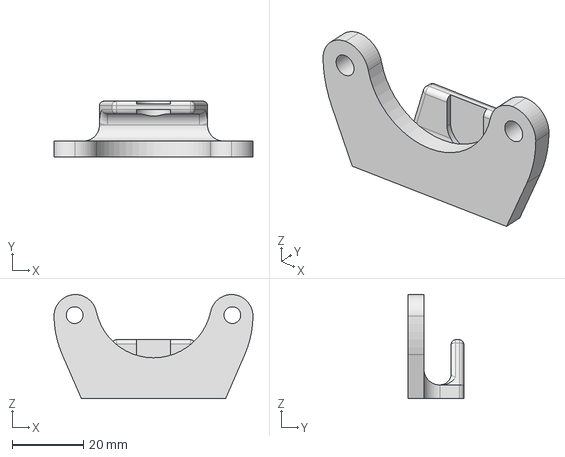
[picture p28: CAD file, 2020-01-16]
design/SWX_model/cameramount_new.stp
55.9 x 15.6 x 29.2 mm

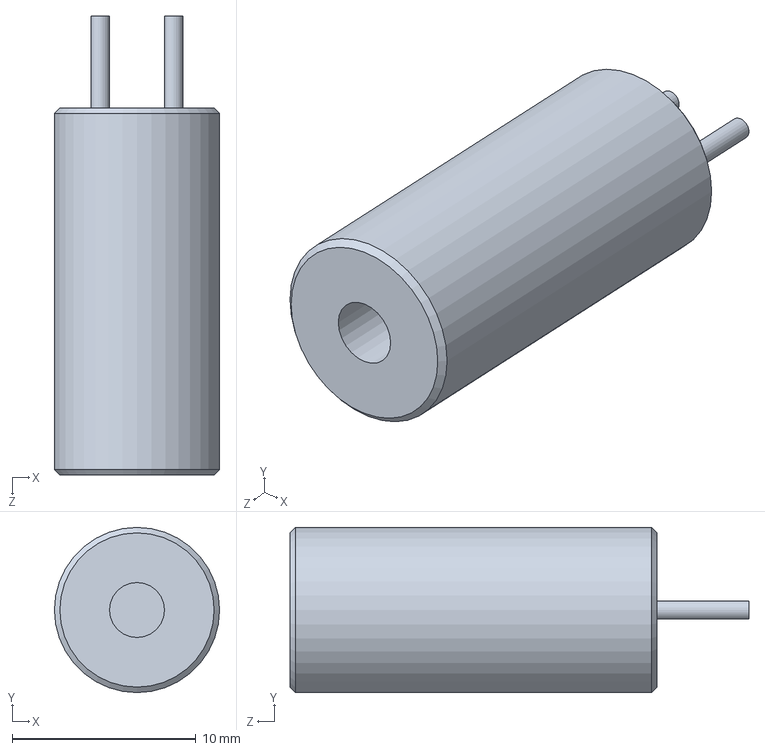
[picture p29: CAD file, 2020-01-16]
design/SWX_model/Lasermodul_LFD650.SLDPRT
9.00 x 9.00 x 25.0 mm

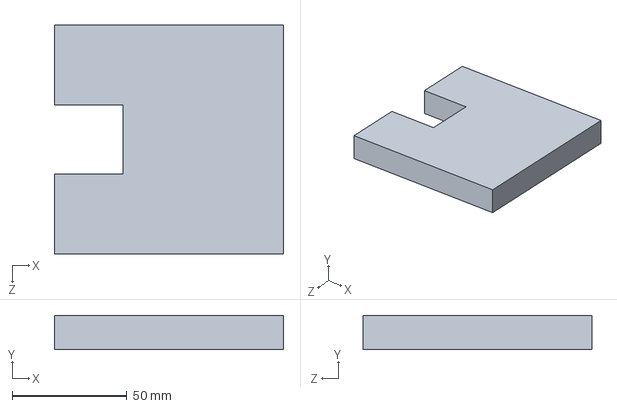
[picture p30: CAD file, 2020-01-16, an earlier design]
design/SWX_model/AKT U 1_copy_copy_copy_copy_copy.SLDPRT
100.0 x 15.0 x 100.0 mm

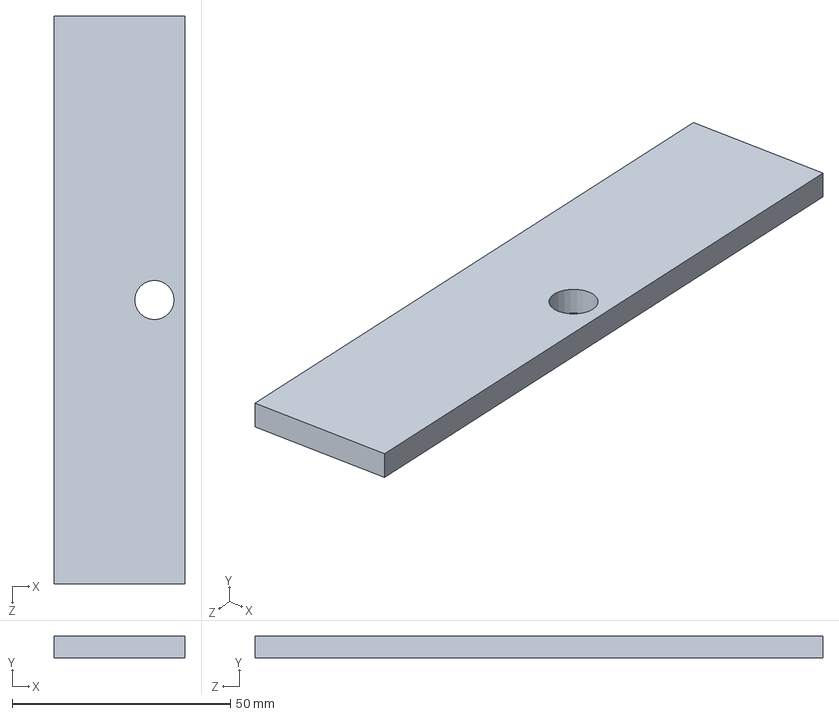
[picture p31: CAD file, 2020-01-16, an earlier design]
design/SWX_model/AKT U 1_copy_copy_copy_copy.SLDPRT
30.0 x 5.00 x 130.0 mm

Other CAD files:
design/SWX_model/AKT U 3x73x46x73x90.SLDPRT
design/drawings/AKT Z 3x40x20x42,5x50.STEP
design/SWX_model/AKT U 3x48x40x48x90.SLDPRT
design/SWX_model/AKT L 3x30x80x30.SLDPRT
design/SWX_model/AKT U 1.SLDPRT
design/SWX_model/AKT U 1_copy.SLDPRT
design/SWX_model/AKT U 1_copy_copy_copy.SLDPRT
design/SWX_model/AKT U 1_copy_copy.SLDPRT
design/SWX_model/AKT L 3x30x80x30.SLDDRW
design/SWX_model/AKT U 1.SLDDRW
design/SWX_model/AKT U 3x48x40x48x90.SLDDRW
design/SWX_model/AKT U 3x73x46x73x90.SLDDRW
design/SWX_model/AKT Z 3x40x20x42,5x50.SLDDRW
design/SWX_model/cameramount_new.SLDPRT
design/drawings/AKT L 3x30x80x30.SLDDRW
design/drawings/AKT L 3x30x80x30.SLDPRT
design/drawings/AKT U 3x48x40x48x90.SLDDRW
design/drawings/AKT U 3x48x40x48x90.SLDPRT
design/drawings/AKT U 3x73x46x73x90.SLDDRW
design/drawings/AKT U 3x73x46x73x90.SLDPRT
design/drawings/AKT Z 3x40x20x42,5x50.SLDDRW

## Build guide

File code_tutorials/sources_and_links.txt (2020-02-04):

# workflow and general structure
https://albertarmea.com/post/opencv-stereo-camera/

# single camera calibration official documentation
https://docs.opencv.org/4.1.0/dc/dbb/tutorial_py_calibration.html

# usage of triangulate 
https://stackoverflow.com/questions/22334023/how-to-calculate-3d-object-points-from-2d-image-points-using-stereo-triangulatio
https://docs.opencv.org/2.4/modules/calib3d/doc/camera_calibration_and_3d_reconstruction.html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

# hand eye calibration with opencv
https://answers.opencv.org/question/204910/calculate-robot-coordinates-from-measured-chessbaord-corners-hand-eye-calibration/

# detect blobs and calculate center of mass
https://www.learnopencv.com/find-center-of-blob-centroid-using-opencv-cpp-python/
https://docs.opencv.org/3.4/d8/da7/structcv_1_1SimpleBlobDetector_1_1Params.html

#template matching
https://opencv-python-tutroals.readthedocs.io/en/latest/py_tutorials/py_imgproc/py_template_matching/py_template_matching.html

# crop image in tkinter
https://stackoverflow.com/questions/55636313/selecting-an-area-of-an-image-with-a-mouse-and-recording-the-dimensions-of-the-s
https://stackoverflow.com/questions/19838972/how-to-update-an-image-on-a-canvas/19842646

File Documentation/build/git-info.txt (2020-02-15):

\gdef\GITHash{3682f08}
\gdef\GITDate{2020-02-14}

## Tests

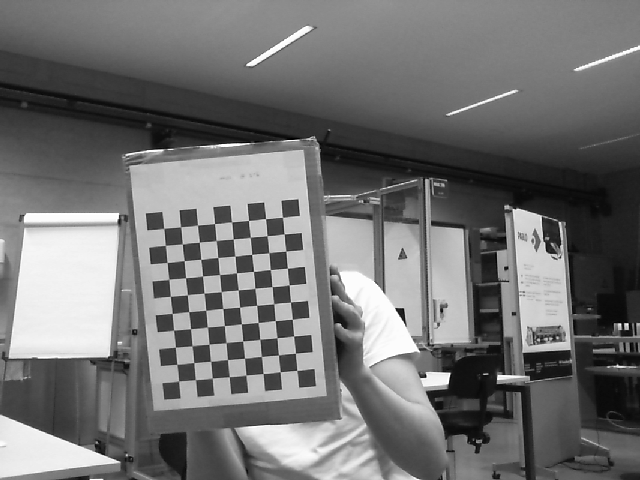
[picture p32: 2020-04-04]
vision/calibration/chessboard_data/camera_left/left_16.png

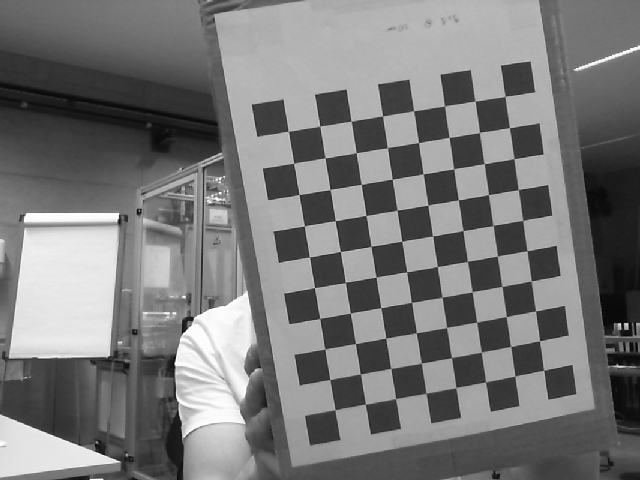
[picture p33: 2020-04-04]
vision/calibration/chessboard_data/camera_left/left_3.png

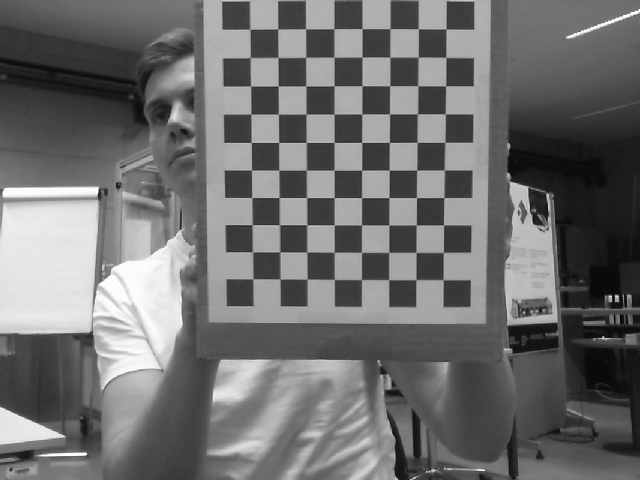
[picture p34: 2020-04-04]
vision/calibration/chessboard_data/camera_right/right_8.png

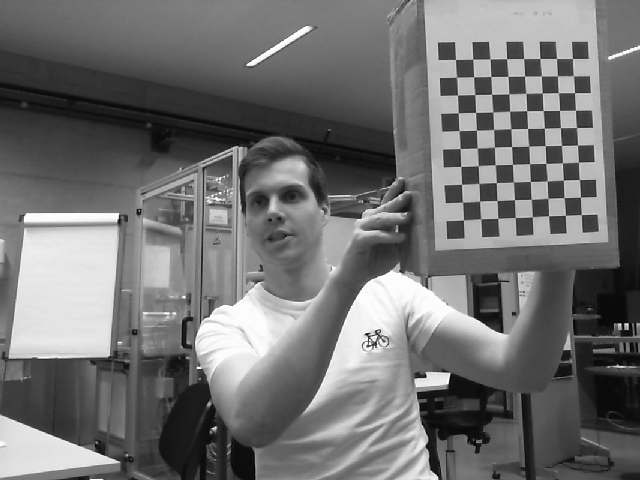
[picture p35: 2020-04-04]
vision/calibration/chessboard_data/camera_left/left_18.png

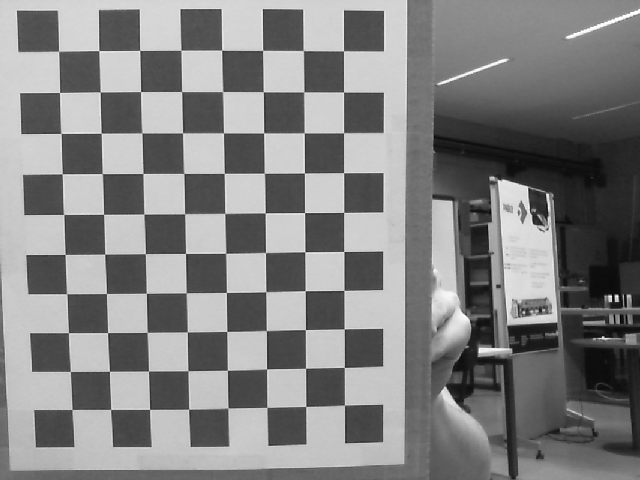
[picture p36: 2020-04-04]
vision/calibration/chessboard_data/camera_right/right_2.png

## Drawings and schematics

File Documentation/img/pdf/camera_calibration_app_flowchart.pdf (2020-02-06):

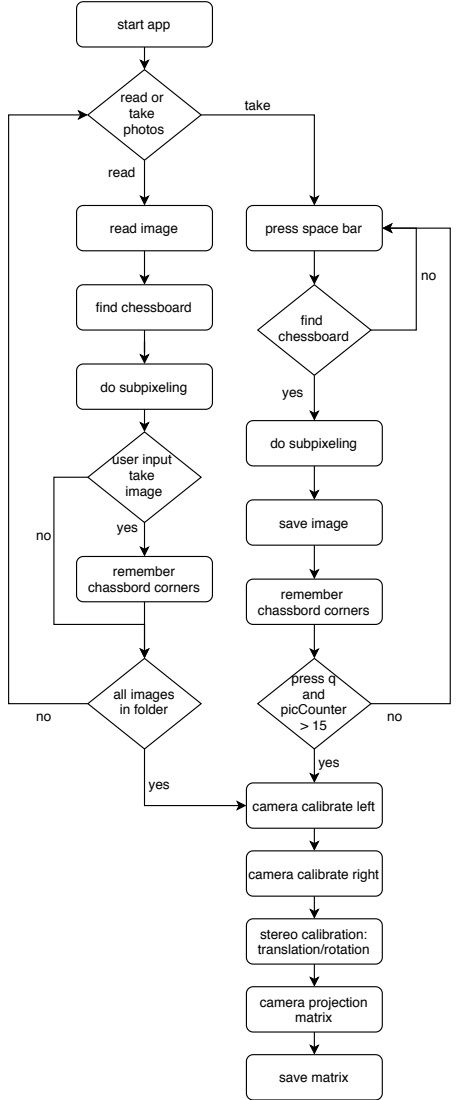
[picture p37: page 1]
start app; read; yes; find chessboard; do subpixeling; save image; press q and picCounter > 15; remember chassbord corners; read image; all images in folder; user input take image; stereo calibration: translation/rotation; camera projection matrix; save matrix

take read or
take
photos

press space bar

camera calibrate left

camera calibrate right

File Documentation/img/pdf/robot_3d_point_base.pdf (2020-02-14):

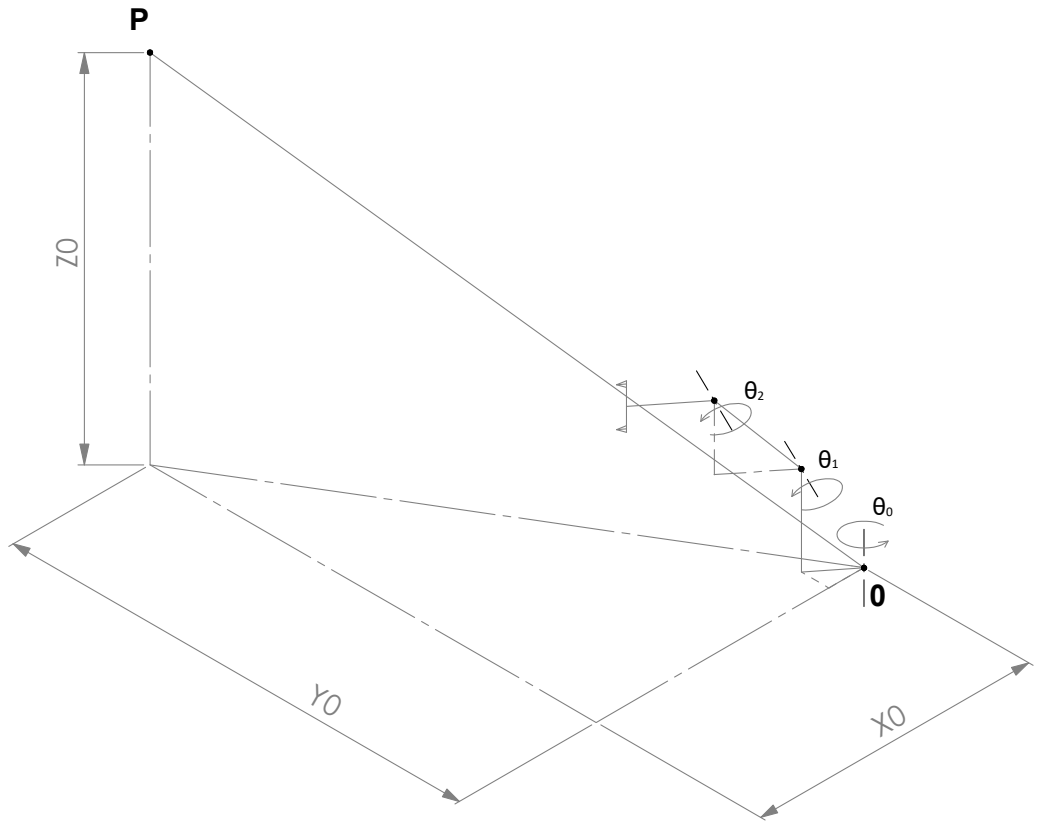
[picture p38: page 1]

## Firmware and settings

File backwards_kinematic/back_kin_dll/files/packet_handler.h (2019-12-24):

/*******************************************************************************
* Copyright 2017 ROBOTIS CO., LTD.
*
* Licensed under the Apache License, Version 2.0 (the "License");
* you may not use this file except in compliance with the License.
* You may obtain a copy of the License at
*
*     http://www.apache.org/licenses/LICENSE-2.0
*
* Unless required by applicable law or agreed to in writing, software
* distributed under the License is distributed on an "AS IS" BASIS,
* WITHOUT WARRANTIES OR CONDITIONS OF ANY KIND, either express or implied.
* See the License for the specific language governing permissions and
* limitations under the License.
*******************************************************************************/

/* Author: Ryu Woon Jung (Leon) */

#ifndef DYNAMIXEL_SDK_INCLUDE_DYNAMIXEL_SDK_PACKETHANDLER_C_H_
#define DYNAMIXEL_SDK_INCLUDE_DYNAMIXEL_SDK_PACKETHANDLER_C_H_


#include <stdio.h>
#include <stdint.h>
#include "robotis_def.h"
#include "port_handler.h"

#define BROADCAST_ID        0xFE    // 254
#define MAX_ID              0xFC    // 252

/* Macro for Control Table Value */
#define DXL_MAKEWORD(a, b)  ((uint16_t)(((uint8_t)(((uint64_t)(a)) & 0xff)) | ((uint16_t)((uint8_t)(((uint64_t)(b)) & 0xff))) << 8))
#define DXL_MAKEDWORD(a, b) ((uint32_t)(((uint16_t)(((uint64_t)(a)) & 0xffff)) | ((uint32_t)((uint16_t)(((uint64_t)(b)) & 0xffff))) << 16))
#define DXL_LOWORD(l)       ((uint16_t)(((uint64_t)(l)) & 0xffff))
#define DXL_HIWORD(l)       ((uint16_t)((((uint64_t)(l)) >> 16) & 0xffff))
#define DXL_LOBYTE(w)       ((uint8_t)(((uint64_t)(w)) & 0xff))
#define DXL_HIBYTE(w)       ((uint8_t)((((uint64_t)(w)) >> 8) & 0xff))

/* Instruction for DXL Protocol */
#define INST_PING           1
#define INST_READ           2
#define INST_WRITE          3
#define INST_REG_WRITE      4
#define INST_ACTION         5
#define INST_FACTORY_RESET  6
#define INST_SYNC_WRITE     131     // 0x83
#define INST_BULK_READ      146     // 0x92
// --- Only for 2.0 --- //
#define INST_REBOOT         8
#define INST_CLEAR          16      // 0x10
#define INST_STATUS         85      // 0x55
#define INST_SYNC_READ      130     // 0x82
#define INST_BULK_WRITE     147     // 0x93

// Communication Result
#define COMM_SUCCESS        0       // tx or rx packet communication success
#define COMM_PORT_BUSY      -1000   // Port is busy (in use)
#define COMM_TX_FAIL        -1001   // Failed transmit instruction packet
#define COMM_RX_FAIL        -1002   // Failed get status packet
#define COMM_TX_ERROR       -2000   // Incorrect instruction packet
#define COMM_RX_WAITING     -3000   // Now recieving status packet
#define COMM_RX_TIMEOUT     -3001   // There is no status packet
#define COMM_RX_CORRUPT     -3002   // Incorrect status packet
#define COMM_NOT_AVAILABLE  -9000   //

typedef struct
{
  uint8_t     *data_write;
  uint8_t     *data_read;
  uint8_t     *tx_packet;
  uint8_t     *rx_packet;
  uint8_t     error;
  int         communication_result;
  uint8_t     *broadcast_ping_id_list;
}PacketData;

PacketData *packetData;

void        packetHandler       ();

const char *getTxRxResult       (int protocol_version, int result);
const char *getRxPacketError    (int protocol_version, uint8_t error);

int         getLastTxRxResult   (int port_num, int protocol_version);
uint8_t     getLastRxPacketError    (int port_num, int protocol_version);

void        setDataWrite        (int port_num, int protocol_version, uint16_t data_length, uint16_t data_pos, uint32_t data);
uint32_t    getDataRead         (int port_num, int protocol_version, uint16_t data_length, uint16_t data_pos);

void        txPacket            (int port_num, int protocol_version);

void        rxPacket            (int port_num, int protocol_version);

void        txRxPacket          (int port_num, int protocol_version);

void        ping                (int port_num, int protocol_version, uint8_t id);

uint16_t    pingGetModelNum     (int port_num, int protocol_version, uint8_t id);

// broadcastPing
void        broadcastPing       (int port_num, int protocol_version);
uint8_t     getBroadcastPingResult  (int port_num, int protocol_version, int id);

void        reboot              (int port_num, int protocol_version, uint8_t id);

void        clearMultiTurn      (int port_num, int protocol_version, uint8_t id);

void        factoryReset        (int port_num, int protocol_version, uint8_t id, uint8_t option);

void        readTx              (int port_num, int protocol_version, uint8_t id, uint16_t address, uint16_t length);
void        readRx              (int port_num, int protocol_version, uint16_t length);
void        readTxRx            (int port_num, int protocol_version, uint8_t id, uint16_t address, uint16_t length);

void        read1ByteTx         (int port_num, int protocol_version, uint8_t id, uint16_t address);
uint8_t     read1ByteRx         (int port_num, int protocol_version);
uint8_t     read1ByteTxRx       (int port_num, int protocol_version, uint8_t id, uint16_t address);

void        read2ByteTx         (int port_num, int protocol_version, uint8_t id, uint16_t address);
uint16_t    read2ByteRx         (int port_num, int protocol_version);
uint16_t    read2ByteTxRx       (int port_num, int protocol_version, uint8_t id, uint16_t address);

void        read4ByteTx         (int port_num, int protocol_version, uint8_t id, uint16_t address);
uint32_t    read4ByteRx         (int port_num, int protocol_version);
uint32_t    read4ByteTxRx       (int port_num, int protocol_version, uint8_t id, uint16_t address);

void    writeTxOnly             (int port_num, int protocol_version, uint8_t id, uint16_t address, uint16_t length);
void    writeTxRx               (int port_num, int protocol_version, uint8_t id, uint16_t address, uint16_t length);

void    write1ByteTxOnly        (int port_num, int protocol_version, uint8_t id, uint16_t address, uint8_t data);
void    write1ByteTxRx          (int port_num, int protocol_version, uint8_t id, uint16_t address, uint8_t data);

void    write2ByteTxOnly        (int port_num, int protocol_version, uint8_t id, uint16_t address, uint16_t data);
void    write2ByteTxRx          (int port_num, int protocol_version, uint8_t id, uint16_t address, uint16_t data);

void    write4ByteTxOnly        (int port_num, int protocol_version, uint8_t id, uint16_t address, uint32_t data);
void    write4ByteTxRx          (int port_num, int protocol_version, uint8_t id, uint16_t address, uint32_t data);

void    regWriteTxOnly          (int port_num, int protocol_version, uint8_t id, uint16_t address, uint16_t length);
void    regWriteTxRx            (int port_num, int protocol_version, uint8_t id, uint16_t address, uint16_t length);

void    syncReadTx              (int port_num, int protocol_version, uint16_t start_address, uint16_t data_length, uint16_t param_length);
// syncReadRx   -> GroupSyncRead
// syncReadTxRx -> GroupSyncRead
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

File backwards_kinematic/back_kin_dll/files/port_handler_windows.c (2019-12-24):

/*******************************************************************************
* Copyright 2017 ROBOTIS CO., LTD.
*
* Licensed under the Apache License, Version 2.0 (the "License");
* you may not use this file except in compliance with the License.
* You may obtain a copy of the License at
*
*     http://www.apache.org/licenses/LICENSE-2.0
*
* Unless required by applicable law or agreed to in writing, software
* distributed under the License is distributed on an "AS IS" BASIS,
* WITHOUT WARRANTIES OR CONDITIONS OF ANY KIND, either express or implied.
* See the License for the specific language governing permissions and
* limitations under the License.
*******************************************************************************/

/* Author: Ryu Woon Jung (Leon) */

#if defined(_WIN32) || defined(_WIN64)

#include <stdio.h>
#include <string.h>
#include <time.h>
#include "port_handler_windows.h"

#define LATENCY_TIMER  16 // msec (USB latency timer)
                          // You should adjust the latency timer value. In Windows, the default latency timer of the usb serial is '16 msec'.
                          // When you are going to use sync / bulk read, the latency timer should be loosen.
                          // the lower latency timer value, the faster communication speed.

                          // Note:
                          // You can either checking or changing its value by:
                          // [Device Manager] -> [Port (COM & LPT)] -> the port you use but starts with COMx-> mouse right click -> properties
                          // -> [port settings] -> [details] -> change response time from 16 to the value you need

typedef struct
{
  HANDLE  serial_handle;
  LARGE_INTEGER freq, counter;

  int     baudrate;
  char    port_name[100];

  double  packet_start_time;
  double  packet_timeout;
  double  tx_time_per_byte;
}PortData;

static PortData *portData;

int portHandlerWindows(const char *port_name)
{
  int port_num;
  char buffer[15];

  sprintf_s(buffer, sizeof(buffer), "\\\\.\\%s", port_name);

  if (portData == NULL)
  {
    port_num = 0;
    g_used_port_num = 1;
    portData = (PortData*)calloc(1, sizeof(PortData));
    g_is_using = (uint8_t*)calloc(1, sizeof(uint8_t));
  }
  else
  {
    for (port_num = 0; port_num < g_used_port_num; port_num++)
    {
      if (!strcmp(portData[port_num].port_name, buffer))
        break;
    }

    if (port_num == g_used_port_num)
    {
      for (port_num = 0; port_num < g_used_port_num; port_num++)
      {
        if (portData[port_num].serial_handle != INVALID_HANDLE_VALUE)
          break;
      }

      if (port_num == g_used_port_num)
      {
        g_used_port_num++;
        portData = (PortData*)realloc(portData, g_used_port_num * sizeof(PortData));
        g_is_using = (uint8_t*)realloc(g_is_using, g_used_port_num * sizeof(uint8_t));
      }
    }
    else
    {
      printf("[PortHandler setup] The port number %d has same device name... reinitialize port number %d!!\n", port_num, port_num);
    }
  }

  portData[port_num].serial_handle = INVALID_HANDLE_VALUE;
  portData[port_num].baudrate = DEFAULT_BAUDRATE;
  portData[port_num].packet_start_time = 0.0;
  portData[port_num].packet_timeout = 0.0;
  portData[port_num].tx_time_per_byte = 0.0;

  g_is_using[port_num] = False;

  setPortNameWindows(port_num, buffer);

  return port_num;
}

uint8_t openPortWindows(int port_num)
{
  return setBaudRateWindows(port_num, portData[port_num].baudrate);
}

void closePortWindows(int port_num)
{
  if (portData[port_num].serial_handle != INVALID_HANDLE_VALUE)
  {
    CloseHandle(portData[port_num].serial_handle);
    portData[port_num].serial_handle = INVALID_HANDLE_VALUE;
  }
}

void clearPortWindows(int port_num)
{
  PurgeComm(portData[port_num].serial_handle, PURGE_RXABORT | PURGE_RXCLEAR);
}

void setPortNameWindows(int port_num, const char *port_name)
{
  strcpy_s(portData[port_num].port_name, sizeof(portData[port_num].port_name), port_name);
}

char *getPortNameWindows(int port_num)
{
  return portData[port_num].port_name;
}

uint8_t setBaudRateWindows(int port_num, const int baudrate)
{
  closePortWindows(port_num);

  portData[port_num].baudrate = baudrate;
  return setupPortWindows(port_num, baudrate);
}

int getBaudRateWindows(int port_num)
{
  return portData[port_num].baudrate;
}

int readPortWindows(int port_num, uint8_t *packet, int length)
{
  DWORD dwRead = 0;

  if (ReadFile(portData[port_num].serial_handle, packet, (DWORD)length, &dwRead, NULL) == FALSE)
    return -1;

  return (int)dwRead;
}

int writePortWindows(int port_num, uint8_t *packet, int length)
{
  DWORD dwWrite = 0;

  if (WriteFile(portData[port_num].serial_handle, packet, (DWORD)length, &dwWrite, NULL) == FALSE)
    return -1;

  return (int)dwWrite;
}

void setPacketTimeoutWindows(int port_num, uint16_t packet_length)
{
  portData[port_num].packet_start_time = getCurrentTimeWindows(port_num);
  portData[port_num].packet_timeout = (portData[port_num].tx_time_per_byte * (double)packet_length) + (LATENCY_TIMER * 2.0) + 2.0;
}

void setPacketTimeoutMSecWindows(int port_num, double msec)
{
  portData[port_num].packet_start_time = getCurrentTimeWindows(port_num);
  portData[port_num].packet_timeout = msec;
}

uint8_t isPacketTimeoutWindows(int port_num)
{
  if (getTimeSinceStartWindows(port_num) > portData[port_num].packet_timeout)
  {
    portData[port_num].packet_timeout = 0;
    return True;
  }
  return False;
}

double getCurrentTimeWindows(int port_num)
{
  QueryPerformanceCounter(&portData[port_num].counter);
  QueryPerformanceFrequency(&portData[port_num].freq);
  return (double)portData[port_num].counter.QuadPart / (double)portData[port_num].freq.QuadPart * 1000.0;
}

double getTimeSinceStartWindows(int port_num)
{
  double time_since_start;

  time_since_start = getCurrentTimeWindows(port_num) - portData[port_num].packet_start_time;
  if (time_since_start < 0.0)
    portData[port_num].packet_start_time = getCurrentTimeWindows(port_num);

  return time_since_start;
}
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

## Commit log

2019-11-09 added bk project
    [backwards_kinematic_test.sdf]
2019-11-10 dynamixel motor c library
2019-11-22 bk implementation
    [backwards_kinematic_test.sdf]
2019-12-29 stereo camera calibration app
2020-01-16 async back kin
    [3AchsRoboter.SLDASM, AKT L 3x30x80x30.SLDDRW, AKT L 3x30x80x30.SLDPRT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]
2020-01-28 detect laser dot
2020-02-14 documentation finished
    [3AchsRoboter.SLDASM, AKT L 3x30x80x30.SLDDRW, AKT L 3x30x80x30.SLDPRT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]
2020-02-15 doc: motor parameter table
